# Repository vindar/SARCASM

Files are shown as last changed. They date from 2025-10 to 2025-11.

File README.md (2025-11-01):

# S.A.R.C.A.S.M
**Slightly Annoying Rubik's Cube Automatic Solving Machine**

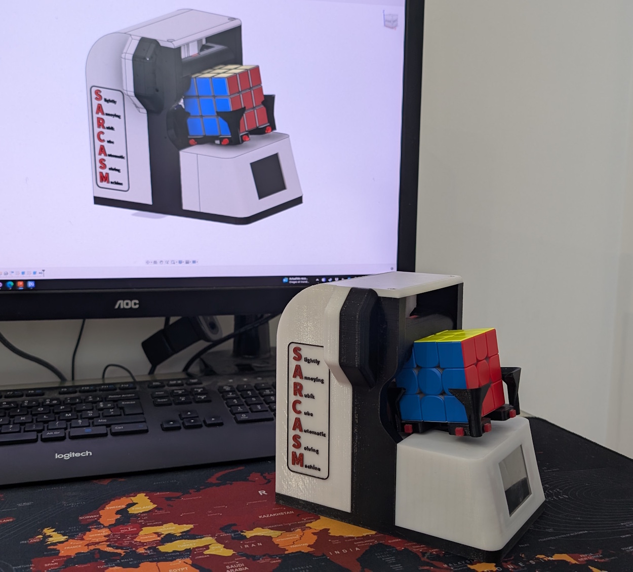
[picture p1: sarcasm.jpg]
S.A.R.C.A.S.M


*S.A.R.C.A.S.M* is a 3D-printed, Teensy-powered robot that scans, solves, and sassily comments on a Rubik’s Cube.  

This repository contains the code and schematics of the build.

Additional details may be found on the Teensy forum thread:

https://forum.pjrc.com/index.php?threads/sarcasm-an-over-engineered-rubiks-cube-solving-robot.77338/

## Demo videos
- Short clip: https://youtube.com/shorts/Xer4mPZZH8E
- Full demo: https://youtu.be/WV52RtuWXk0

## Highlights
- Teensy 4.1 main controller + ESP32-CAM for image capture.
- ILI9341 display with custom 2D&3D graphics, animations, and lip-sync.
- Stepper + servos for cube handling with position sensors to detect faults.  
- RGBW lighting synchronized to audio.
- On-device TTS (espeak-ng) with a collection of sarcastic lines.
- ...

## Note
A slight modification of Teensy's core is required in order for the whole code to fit in RAM. 

Edit `cores/teensy4/usb_serial.c` and `cores/teensy4/usb_serial2.c` and, in each file, remove the DMAMEM attribute in front of the definition of the `txbuffer[]` and `rx_buffer[]` arrays. 

## Warning
This is a work in progress. The repo is currently in a very messy and incomplete state (and will most likely stay that way until I find some time to work on it...). Sorry !

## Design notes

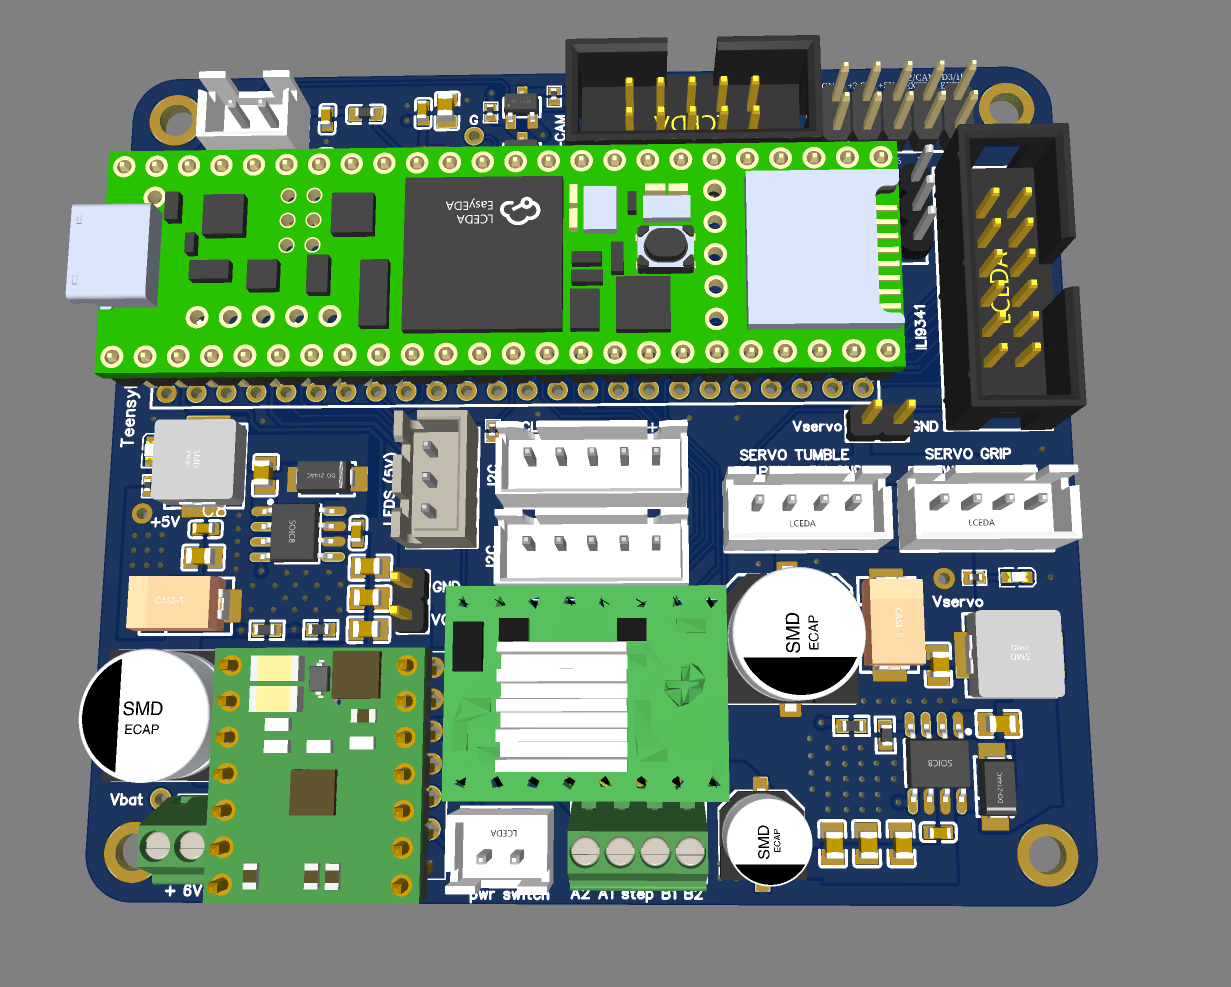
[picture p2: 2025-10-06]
Hardware/mainboard/3D.png

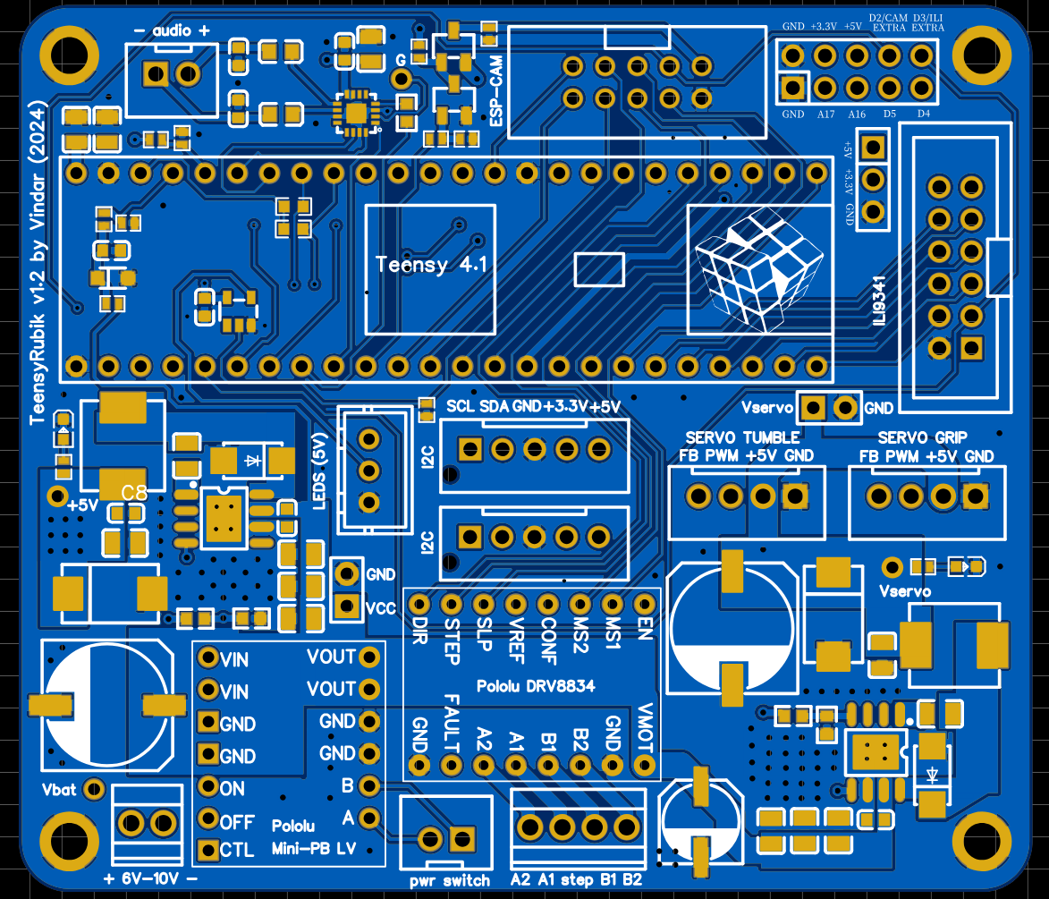
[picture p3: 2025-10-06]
Hardware/mainboard/Capture d'écran 2025-10-04 122526.png

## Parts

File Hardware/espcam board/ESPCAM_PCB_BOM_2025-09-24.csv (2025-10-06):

ID | Name | Designator | Footprint | Quantity | Manufacturer Part | Manufacturer | Supplier | Supplier Part | Price
1 | 68uF | C1,C3 | CAP-SMD_L6.0-W3.2-R-RD | 2 | TAJC686K016RNJ | Kyocera AVX | LCSC | C7220 | 0.317
2 | ESP32-CAM | CAM1 | ESP32CAM-SOCKET | 1 | https://github.com/raphaelbs/esp32-cam-ai-thinker | AI Thinker |  | https://github.com/raphaelbs/esp32-cam-ai-thinker
3 | KT-0603R | LED1 | LED0603-RD | 1 | KT-0603R | KENTO | LCSC | C2286 | 0.006
4 | IDC 2x5 | P1 | IDC-TH_10P-P2.54_C5665 | 1 | IDC Box 2.54mm 2X5P | BOOMELE | LCSC | C5665 | 0.075
5 | 2kΩ | R2 | R0402 | 1 | 0402WGF2001TCE | UNI-ROYAL(厚声) | LCSC | C4109 | 0.001
6 | 10K | R4 | R0603 | 1 | 0603WAF1002T5E | UniOhm | LCSC | C25804 | 0.001
7 | INMP441-MEMS-I2S-MIC-MODULE | U1 | INMP441-MEMS-I2S-MIC-MODULE | 1 |  |  | ebay

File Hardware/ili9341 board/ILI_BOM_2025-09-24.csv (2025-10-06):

ID | Name | Designator | Footprint | Quantity | Manufacturer Part | Manufacturer | Supplier | Supplier Part | Price
1 | 470uF | C5 | CAP-TH_BD8.0-P3.50-D1.0-FD | 1 | 01EC1227SHC470UF25V | KNSCHA | LCSC | C503221 | 0.053
2 | HDR 2.54mm 1x14 | CON1 | HDR 2.54MM 1X14 | 1 | HDR 2.54mm 1x14
3 | green | LED2 | LED0603-R-RD | 1 | 19-217/GHC-YR1S2/3T | EVERLIGHT | LCSC | C72043 | 0.022
4 | IDC 2x6 | P1 | IDC-TH_12P-P2.54_BOOMELE-2X6P-2.54MM | 1 | IDC Box 2X6 2.54MM | BOOMELE | LCSC | C9136 | 0.096
5 | 2K | R2 | R0603 | 1 | 0603WAF2001T5E | UniOhm | LCSC | C22975 | 0.001

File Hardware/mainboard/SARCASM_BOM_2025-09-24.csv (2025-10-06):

ID | Name | Designator | Footprint | Quantity | Manufacturer Part | Manufacturer | Supplier | Supplier Part | Price | JLCPCB Part Class | LCSC Assembly
1 | 100nF | C1,C21 | C0603 | 2 | CC0603KRX7R9BB104 | YAGEO(国巨) | LCSC | C14663 | 0.002 | Basic Part
2 | 22uF | C2,C3,C6,C12,C16,C17,C19,C23,C25,C26,C28 | C0805 | 11 | CL21A226MAQNNNE | SAMSUNG | LCSC | C45783 | 0.025 |  | Yes
3 | 1uF | C4,C5,C7,C8 | C0603 | 4 | CL10A105KB8NNNC | SAMSUNG(三星) | LCSC | C15849 | 0.005 | Basic Part
4 | 470uF | C9,C11 | CAP-SMD_BD10.0-L10.3-W10.3-RD | 2 | VZH471M1ETR-1010 | Lite-On Semicon | LCSC | C249933 | 0.152 |  | Yes
5 | 10nF | C13,C27 | C0805 | 2 | CL21B103KBANNNC | SAMSUNG | LCSC | C1710 | 0.006 |  | Yes
6 | 1nF | C15,C22 | C0603 | 2 | CL10B102KB8NNNC | SAMSUNG(三星) | LCSC | C1588 | 0.003 | Basic Part
7 | 220uF | C18,C24 | CAP-SMD_L7.3-W4.3-R-RD | 2 | 10TPE220ML | PANASONIC | LCSC | C147767 | 0.854 |  | Yes
8 | 100uF | C20 | CAP-SMD_BD6.3-L6.6-W6.6-RD | 1 | VES101M1ETR-0607 | LELON | LCSC | C176675 | 0.055 |  | Yes
9 | JST-XH | CN1,CN4 | CONN-TH_B2B-XH-A (LF)(SN) | 2 | - | JST Sales America | LCSC | C158012 | 0.035
10 | JST-XH | CN2,CN3 | CONN-TH_B5B-XH-AM-LF-SN | 2 | B5B-XH-AM(LF)(SN) | JST | LCSC | C161872 | 0.106 | Extended Part
11 | MM3Z10VST1G | D1 | SOD-323_L1.8-W1.3-LS2.5-RD | 1 | MM3Z10VST1G | ON Semicon | LCSC | C235983 | 0.039 |  | Yes
12 | SS34_C8678 | D2,D3 | DO-214AC_L4.3-W2.7-LS5.3-RD | 2 | SS34 | MDD | LCSC | C8678 | 0.028 |  | Yes
13 | HDR | H1,H2 | HDR-TH_2P-P2.54-V-M-1 | 2 | B-2100S02P-A110 | Ckmtw(灿科盟) | LCSC | C124375 | 0.025 | Extended Part
14 | 10uH | L1,L2 | IND-SMD_L7.1-W6.6 | 2 | MWSA0603-100MT | Sunlord | LCSC | C132141 |  |  | Yes
15 | 220Ω | L3,L4 | L0603 | 2 | MPZ1608S221ATA00 | TDK | LCSC | C76815 | 0.01
16 | KT-0603R | LED2,LED3 | LED0603-RD | 2 | KT-0603R | KENTO | LCSC | C2286 | 0.006 | Basic Part
17 | IDC 2x6 | P1 | IDC-TH_12P-P2.54_BOOMELE-2X6P-2.54MM | 1 | IDC Box 2X6 2.54MM | BOOMELE | LCSC | C9136 | 0.096
18 | IDC 2x5 | P3 | IDC-TH_10P-P2.54_C5665 | 1 | IDC Box 2.54mm 2X5P | BOOMELE | LCSC | C5665 | 0.075
19 | S8050 | Q1 | SOT-23-3_L3.0-W1.7-P0.95-LS2.9-BR | 1 | S8050 | CJ | LCSC | C2146 | 0.013 |  | Yes
20 | SI2301CDS-T1-GE3 | Q3 | SOT-23-3_L3.0-W1.7-P0.95-LS2.9-BR | 1 | SI2301CDS-T1-GE3 | VISHAY | LCSC | C10487 | 0.057 |  | Yes
21 | 10K | R1,R5 | R0402 | 2 | 0402WGF1002TCE | UniOhm | LCSC | C25744 | 0.001 |  | Yes
22 | 2K | R2,R10 | R0402 | 2 | 0402WGF2001TCE | UniOhm | LCSC | C4109 | 0.001 |  | Yes
23 | 33K | R3,R9,R13,R14,R24 | R0402 | 5 | 0402WGF3302TCE | UniOhm | LCSC | C25779 | 0.001 |  | Yes
24 | 1K | R4,R25 | R0402 | 2 | 0402WGF1001TCE | UniOhm | LCSC | C11702 | 0.001 |  | Yes
25 | 22K | R6 | R0402 | 1 | 0402WGF2202TCE | UniOhm | LCSC | C25768 | 0.001 |  | Yes
26 | 3.24K | R7,R20 | R0603 | 2 | 0603WAF3241T5E | UniOhm | LCSC | C22994 | 0.001 |  | Yes
27 | 10K | R8,R19 | R0603 | 2 | 0603WAF1002T5E | UniOhm | LCSC | C25804 | 0.001 |  | Yes
28 | 3kΩ | R11,R12 | R0603 | 2 | 0603WAF3001T5E | UNI-ROYAL(厚声) | LCSC | C4211 | 0.001 | Basic Part
29 | 620K | R22 | R0603 | 1 | 0603WAF6203T5E | UniOhm | LCSC | C23219 | 0.001 |  | Yes
30 | Pololu Mini Pushbutton Power Switch with Reverse Voltage Protection (LV) | U1 | MINI PUSHBUTTON POWER SWITCH WITH REVERSE VOLTAGE PROTECTION | 1
31 | SN74LV1T34DBVR | U3 | SOT-23-5_L2.9-W1.6-P0.95-LS2.8-BR | 1 | SN74LV1T34DBVR | TI(德州仪器) | LCSC | C100024 | 0.059 | Extended Part
32 | TPS5430DDAR | U4,U13 | SOIC-8_L5.0-W4.0-P1.27-LS6.0-BL-EP | 2 | TPS5430DDAR | TI | LCSC | C9864 | 0.35 |  | Yes
33 | Terminal Block | U5 | CONN-TH_P2.54_KF128-2.54-2P | 1 | KF128-2.54-2P | Cixi Kefa Elec | LCSC | C474920 | 0.219
34 | TEENSY4.1 | U6 | TEENSY 4.1 | 1 |  | PJRC
35 | JST-XH | U7 | CONN-TH_B4B-XH-A (LF)(SN) | 1 | B4B-XH-A(LF)(SN) | JST Sales America | LCSC | C144395 | 0.049
36 | JST XH | U8 | CONN-TH_B4B-XH-A (LF)(SN) | 1 | B4B-XH-A(LF)(SN) | JST Sales America | LCSC | C144395 | 0.049
37 | Pololu DRV8834 | U9 | DRV8834 STEPPER MOTOR DRIVER CARRIER | 1
38 | terminal block | U10 | CONN-TH_4P-P2.54_KF128-2.54-4P | 1 | KF128-2.54-4P | Cixi Kefa Elec | LCSC | C474922 | 0.448
39 | HDR | U11 | CONN-TH_3P-P2.50_A2501WV2-3P | 1 | B3B-XH-A(LF)(SN) | JST | LCSC | C144394 | 0.047 | Extended Part
40 | HDR 2x5 | U12 | HDR-TH_10P-P2.54-V-M-R2-C5-S2.54 | 1 | ZX-PZ2.54-2-5PZZ | Megastar(兆星) | LCSC | C7501276 | 0.041 | Extended Part
41 | HDR | U14 | HDR-TH_3P-P2.54-V-M | 1 | HB-PH3-25413PB2GOP | HANBO(汉博) | LCSC | C6332196 | 0.016 | Extended Part
42 | MAX98357AETE+T | U15 | TQFN-16_L3.0-W3.0-P0.50-BL-EP1.5 | 1 | MAX98357AETE+T | ADI(亚德诺)/MAXIM(美信) | LCSC | C910544 | 1.311 | Extended Part

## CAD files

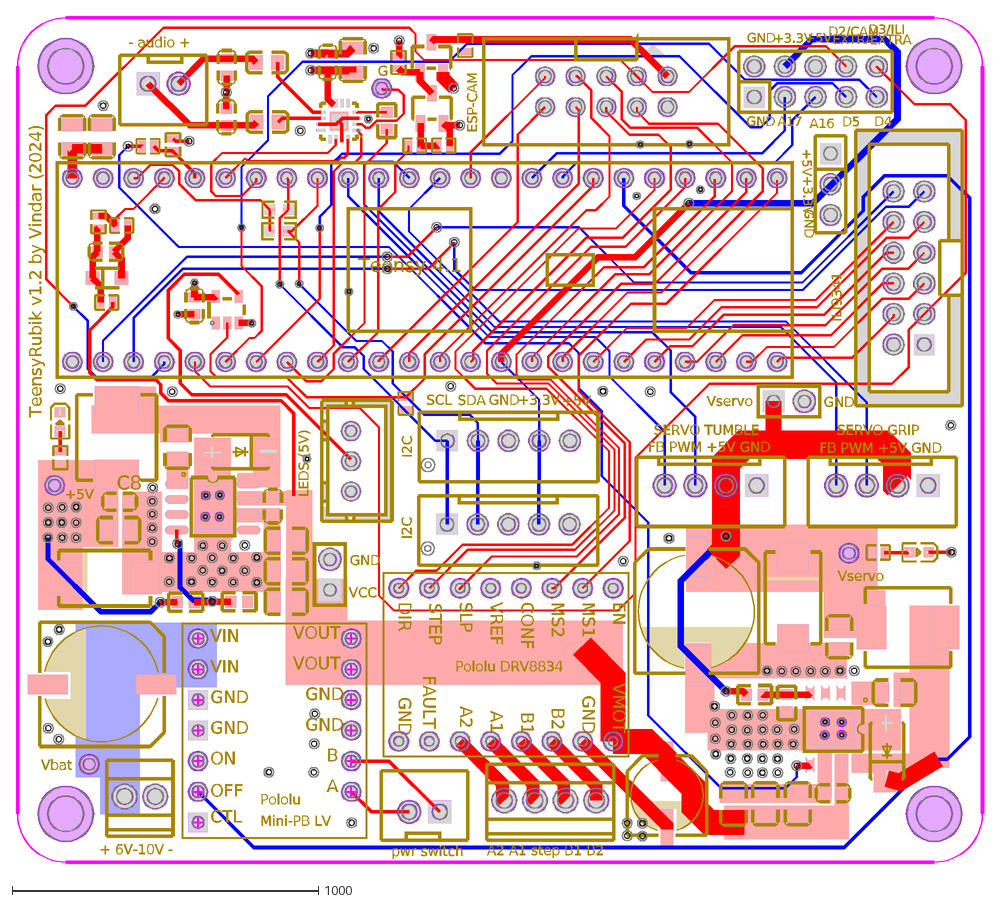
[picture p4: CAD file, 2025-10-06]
Hardware/mainboard/SARCASM_PCB_2025-09-24.dxf
GND
TeensyRubik v1.2 by Vindar (2024)
FB PWM +5V GND
Vservo
- audio +
ILI9341
ESP-CAM
Pololu
Pololu DRV8834
SERVO GRIP
SERVO TUMBLE
A2 A1 step B1 B2
pwr switch
Mini-PB LV
+ 6V-10V -
Vbat
VCC
+5V
Teensy 4.1
+3.3V
D2/CAM
D3/ILI
D4
D5
A17
A16
EXTRA
LEDS (5V)
I2C
SDA
SCL
G
C8
MS1
MS2
CONF
STEP
DIR
FAULT
A2
A1
B1
B2
VMOT
EN
VREF
SLP
VIN
ON
OFF
CTL
A
B
VOUT

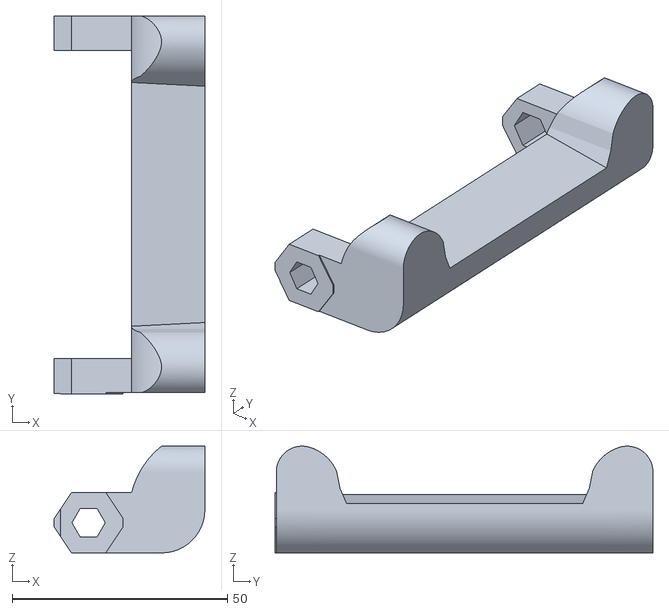
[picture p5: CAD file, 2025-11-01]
Hardware/STL/gripper_main_part.stl
35.0 x 87.8 x 24.8

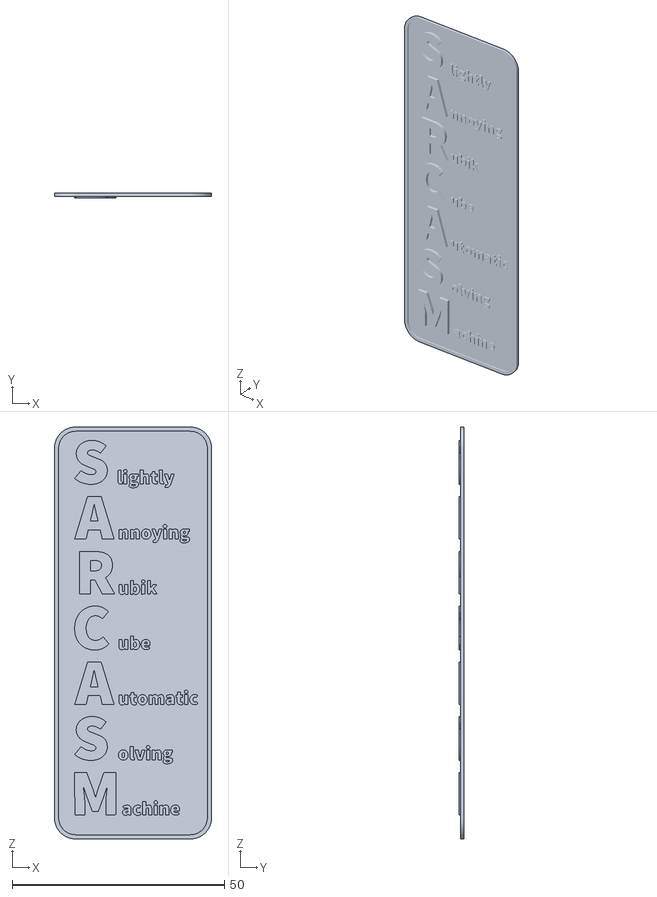
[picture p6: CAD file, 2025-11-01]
Hardware/STL/SARCASM_nametag_multicolor.stl
37.0 x 1.20 x 97.0

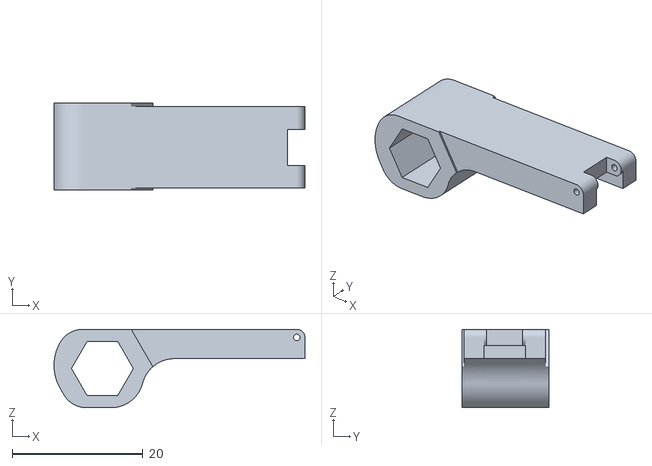
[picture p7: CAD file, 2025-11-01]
Hardware/STL/tumble_lever_main_part.stl
38.4 x 13.2 x 12.0

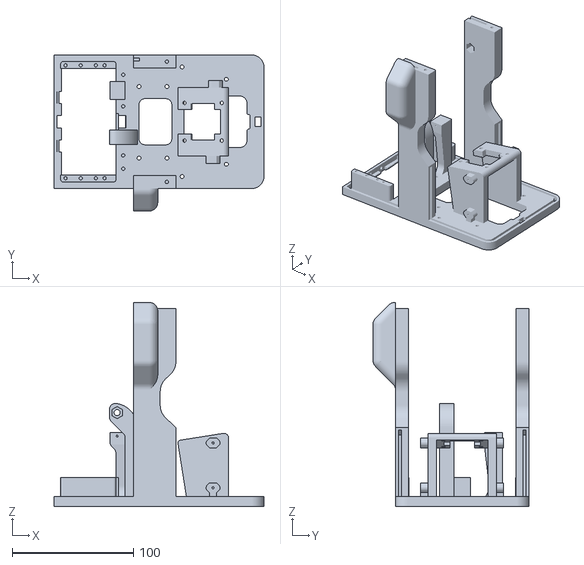
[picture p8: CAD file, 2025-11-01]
Hardware/STL/main_frame.stl
173.0 x 128.5 x 168.1

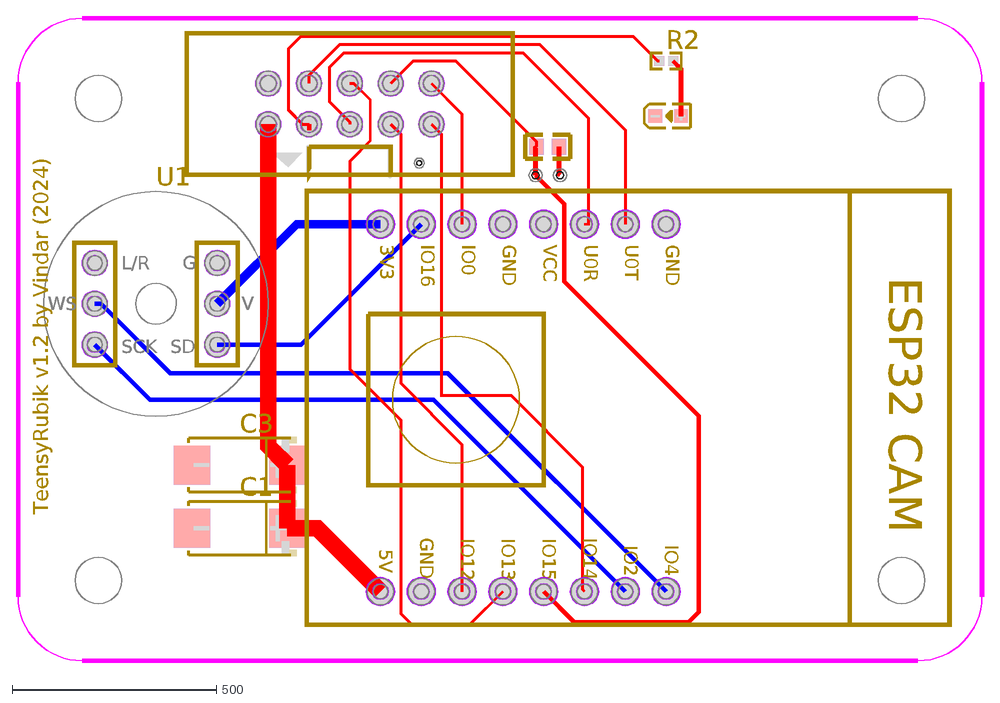
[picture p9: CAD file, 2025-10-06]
Hardware/espcam board/ESPCAM_PCB_2025-09-24.dxf
TeensyRubik v1.2 by Vindar (2024)
C1
C3
R2
U1
G
V
SD
SCK
WS
L/R
GND
ESP32 CAM
U0T
U0R
VCC
IO0
IO16
3V3
5V
IO12
IO13
IO15
IO14
IO2
IO4

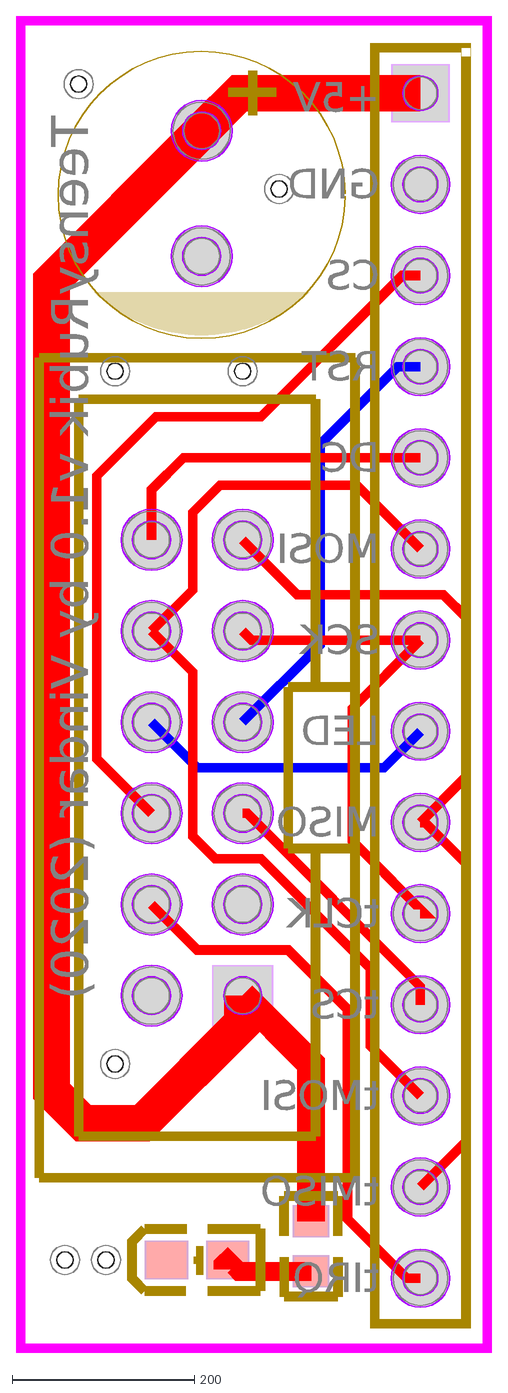
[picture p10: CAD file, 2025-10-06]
Hardware/ili9341 board/ILI9341_PCB_2025-09-24.dxf
TeensyRubik v1.0 by Vindar (2020)
GND
+5V
CS
RST
DC
MOSI
SCK
LED
MISO
tCLK
tCS
tMOSI
tMISO
tIRQ

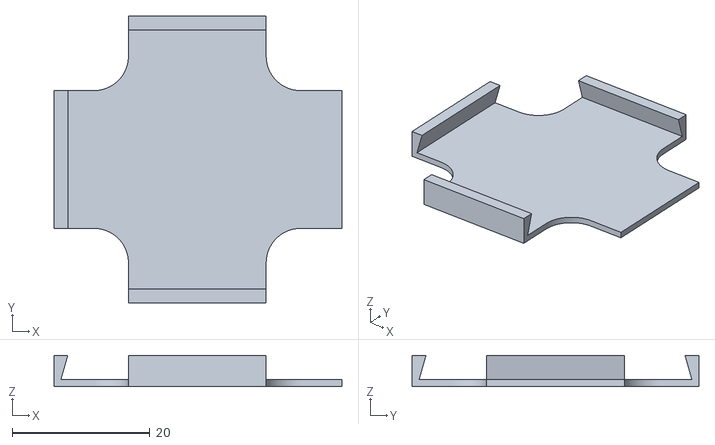
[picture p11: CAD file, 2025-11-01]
Hardware/STL/AS5600_holder_cover.stl
41.8 x 41.6 x 4.50

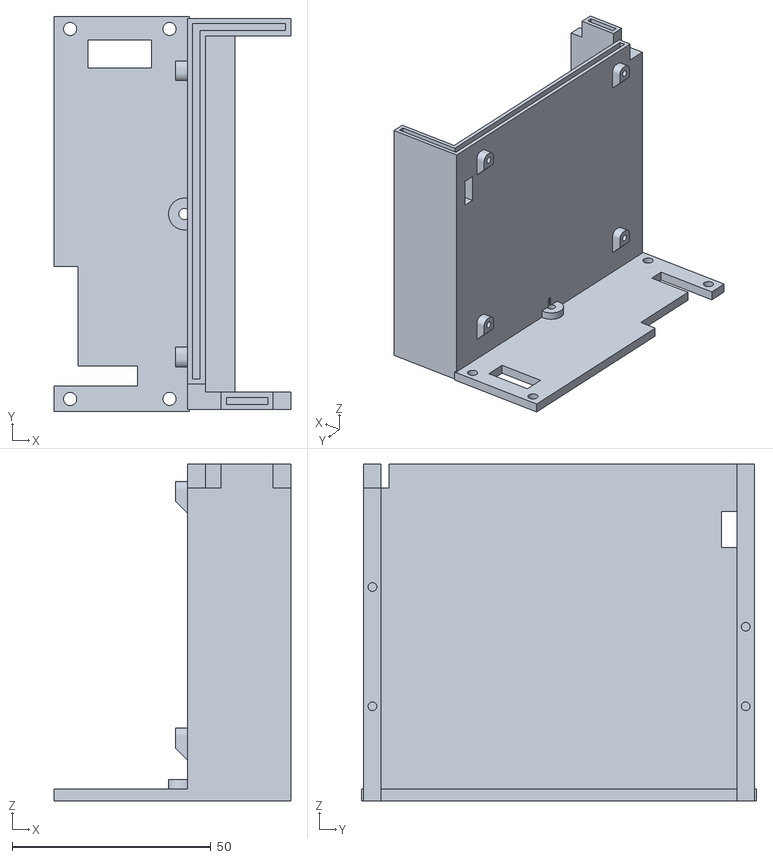
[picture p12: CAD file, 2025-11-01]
Hardware/STL/separator_wall_bottom_part.stl
59.5 x 99.4 x 84.7

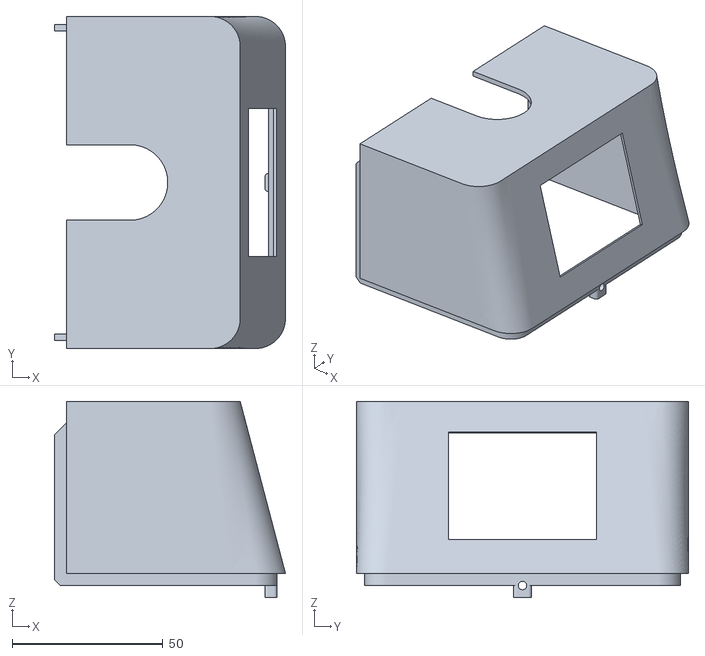
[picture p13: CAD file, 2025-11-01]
Hardware/STL/front_cover.stl
76.5 x 110.0 x 65.0

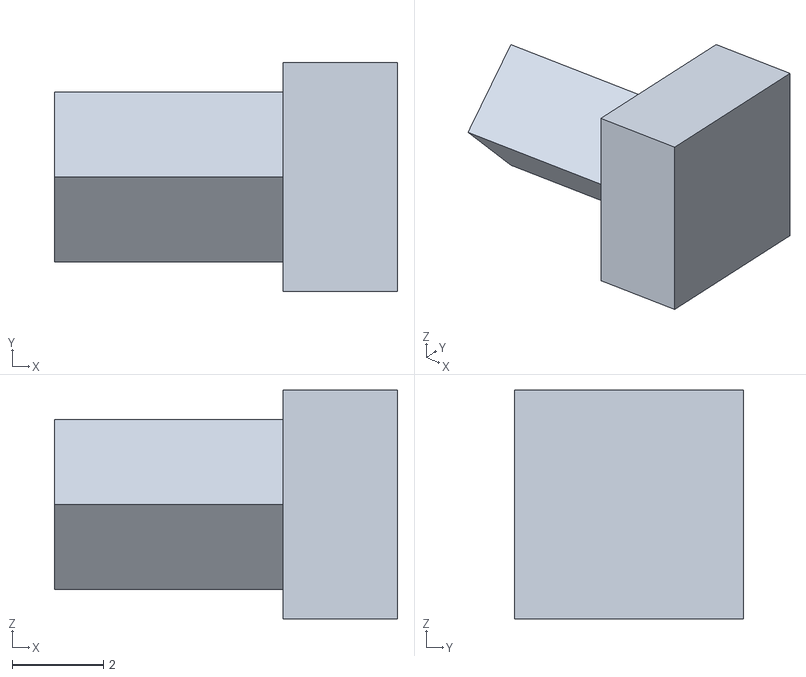
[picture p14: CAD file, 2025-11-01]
Hardware/STL/cube_cradle_red_marker_x8.stl
7.50 x 5.00 x 5.00

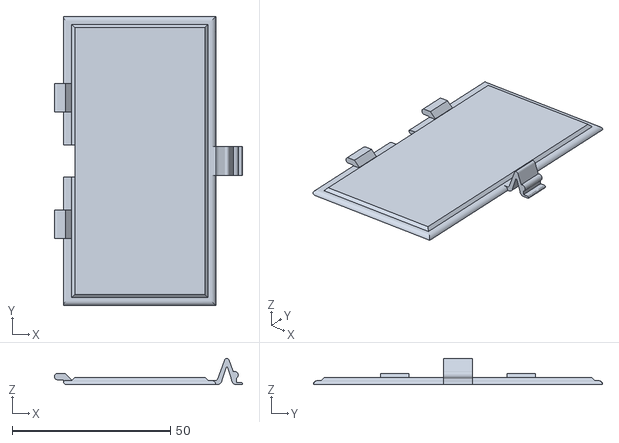
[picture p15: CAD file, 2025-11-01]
Hardware/STL/battery_trap_cover.stl
59.4 x 91.2 x 8.25

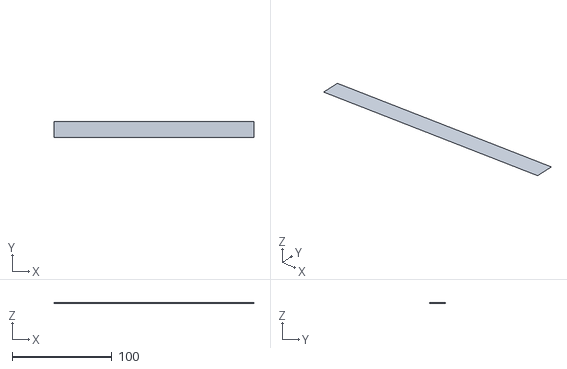
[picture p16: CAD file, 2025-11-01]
Hardware/STL/flexible_led_cover.stl
200.0 x 16.0 x 0.3

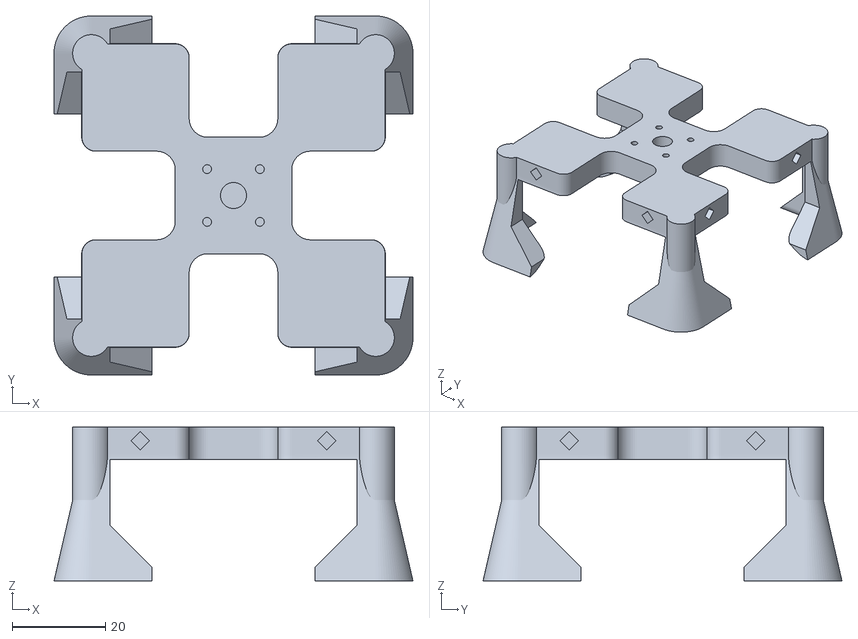
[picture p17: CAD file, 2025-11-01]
Hardware/STL/cube_cradle.stl
77.0 x 77.0 x 33.0

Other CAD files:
Hardware/STL/espcam_arm_right.stl
Hardware/STL/tumble_lever_tip.stl
Hardware/STL/gripper_color_indicator.stl
Hardware/STL/tumble_cover_left.stl
Hardware/STL/AS5600_holder.stl
Hardware/STL/back_cover.stl
Hardware/STL/espcam_arm_left.stl
Hardware/STL/foot_back_TPU_x2.stl
Hardware/STL/foot_front_1_TPU_x2.stl
Hardware/STL/gripper_nut.stl
Hardware/STL/gripper_screw.stl
Hardware/STL/gripper_servo_nut.stl
Hardware/STL/pololu_usb_connector_holder.stl
Hardware/STL/separator_wall_top_part.stl
Hardware/STL/tumble_cover_right.stl
Hardware/STL/tumble_holding_screw.stl
Hardware/STL/tumble_servo_nut.stl

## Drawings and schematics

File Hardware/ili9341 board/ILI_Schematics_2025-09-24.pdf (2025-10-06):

A | A

1

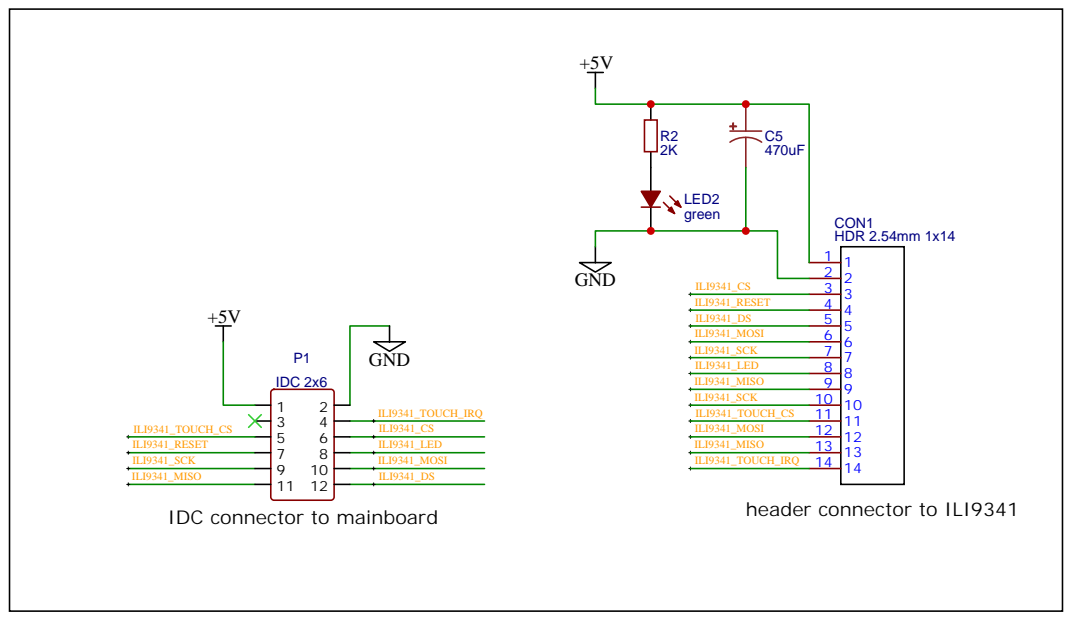
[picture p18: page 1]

ILI9341_SCK
IDC connector to mainboard

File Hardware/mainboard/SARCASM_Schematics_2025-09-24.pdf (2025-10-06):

A | A
B | B

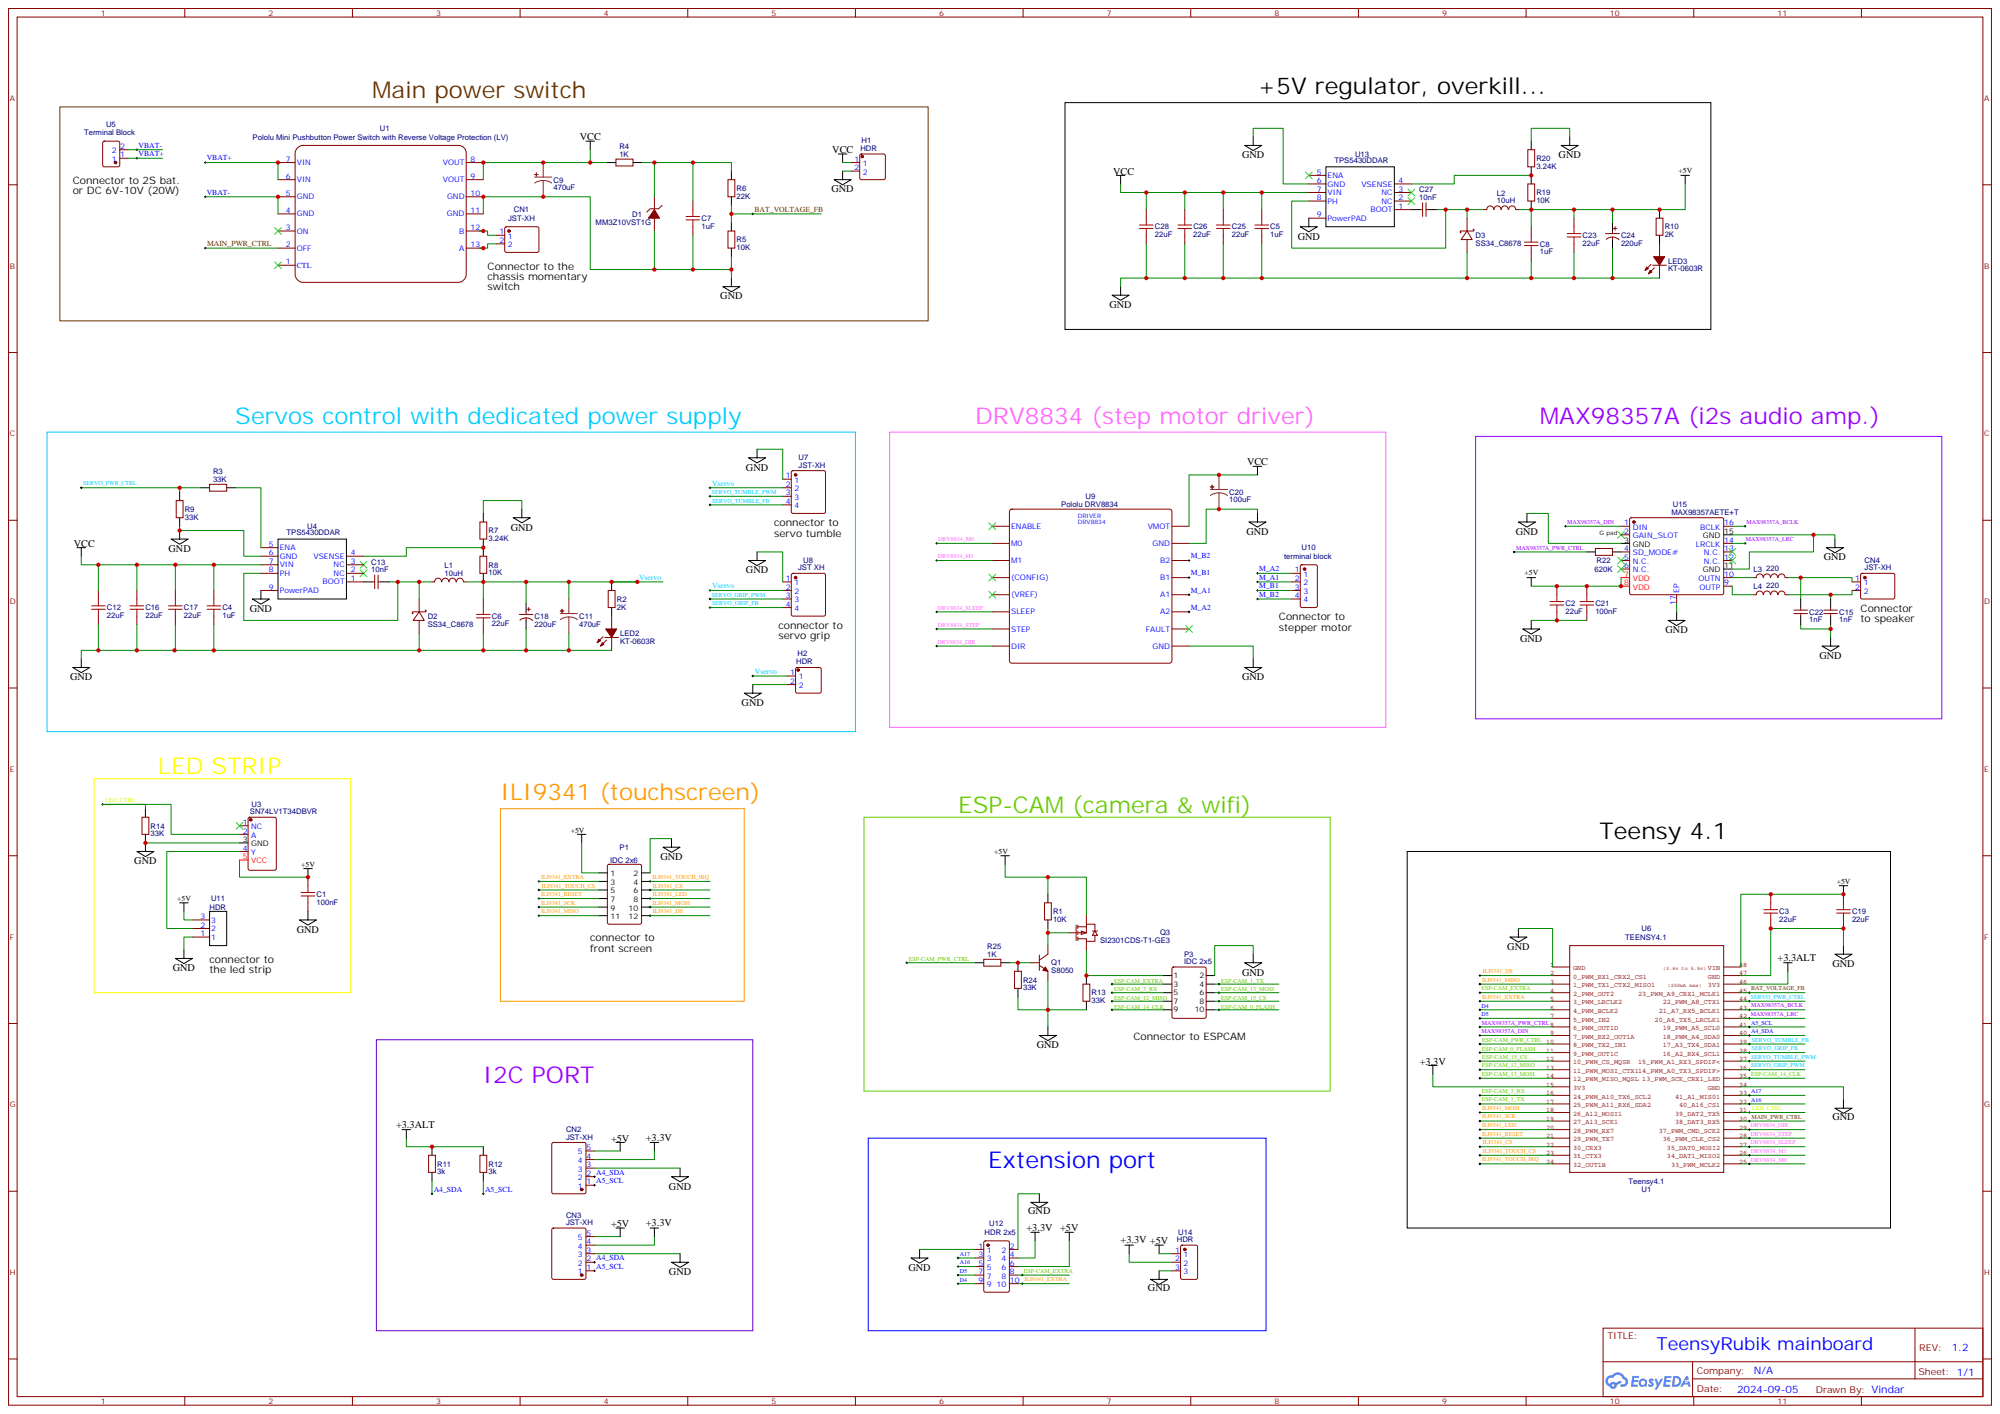
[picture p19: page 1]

Pololu Mini Pushbutton Power Switch with Reverse Voltage Protection (LV)

Servos control with dedicated power supply

ESP-CAM (camera & wifi)

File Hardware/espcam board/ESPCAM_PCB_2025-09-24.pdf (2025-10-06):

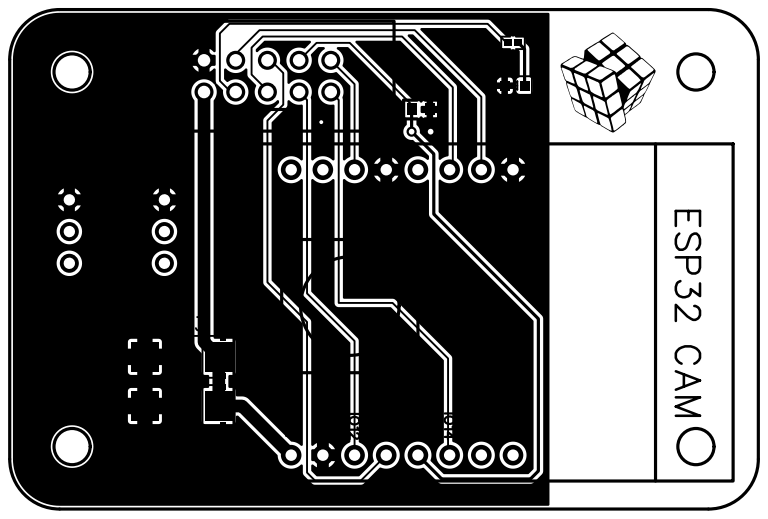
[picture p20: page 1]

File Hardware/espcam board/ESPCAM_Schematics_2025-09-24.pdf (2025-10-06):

A | A

1

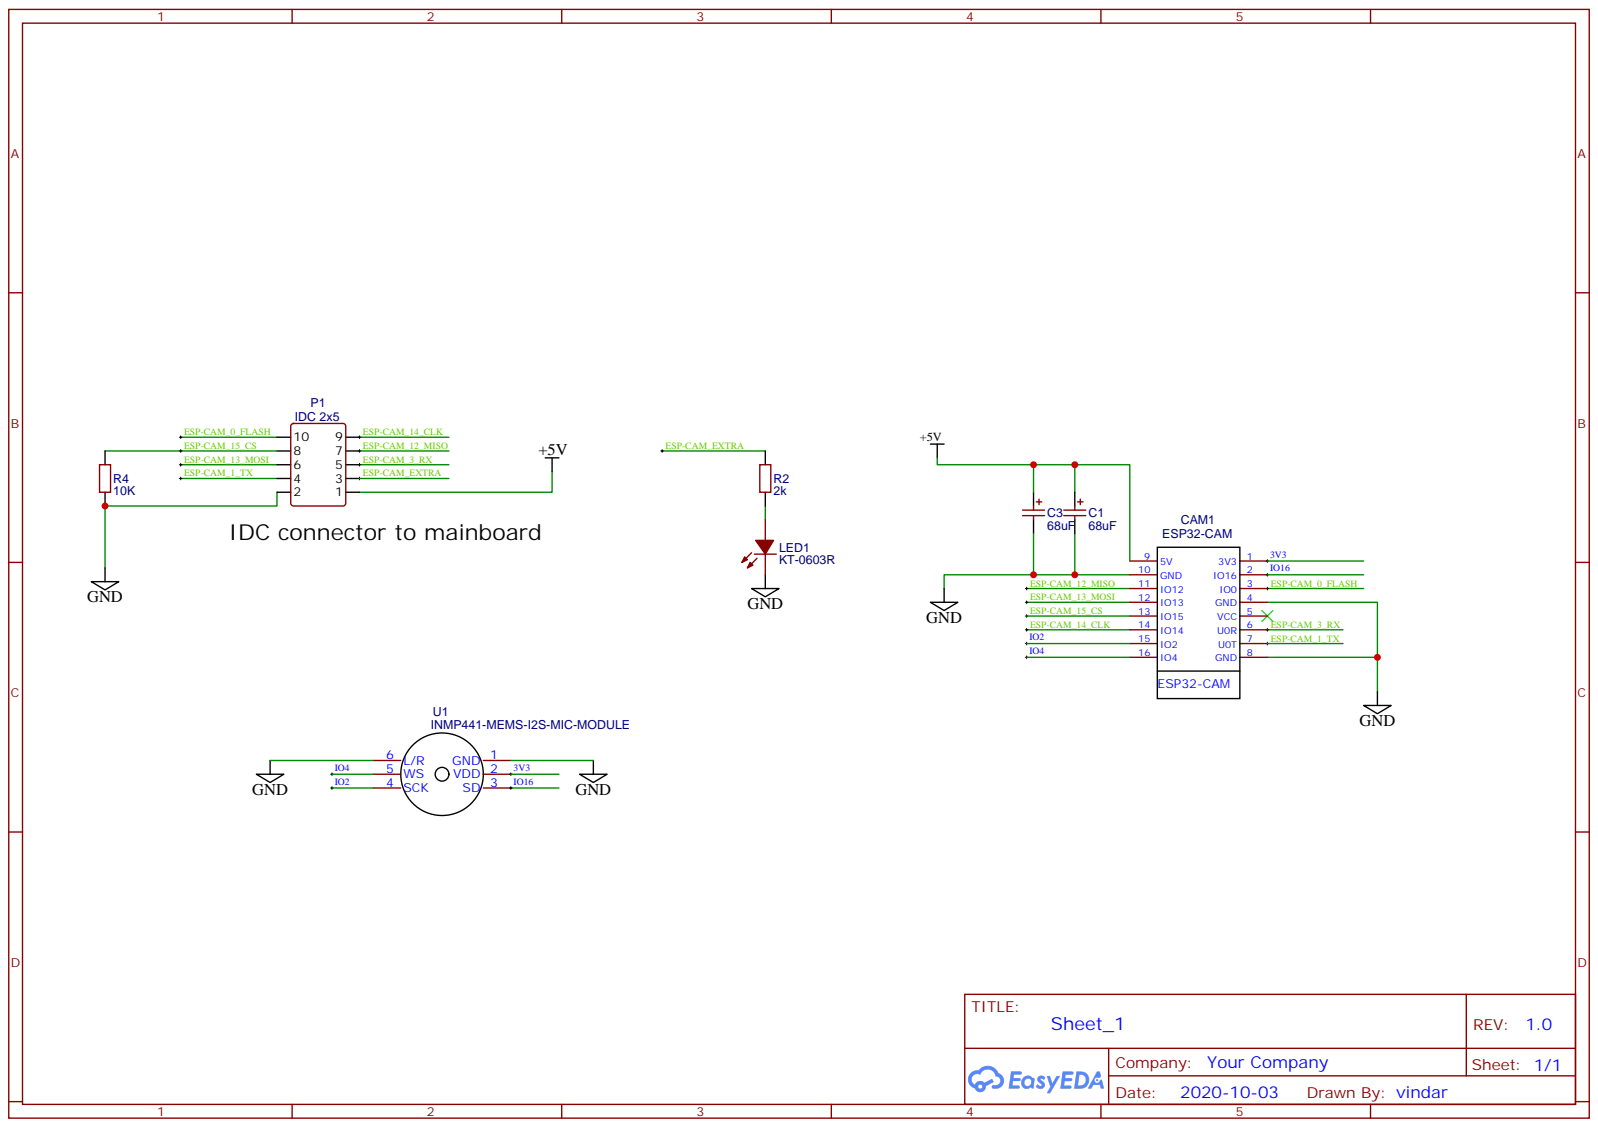
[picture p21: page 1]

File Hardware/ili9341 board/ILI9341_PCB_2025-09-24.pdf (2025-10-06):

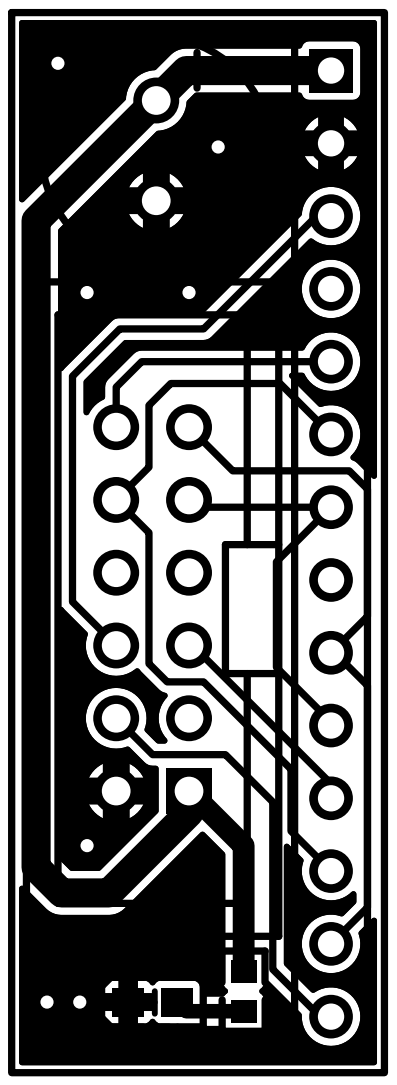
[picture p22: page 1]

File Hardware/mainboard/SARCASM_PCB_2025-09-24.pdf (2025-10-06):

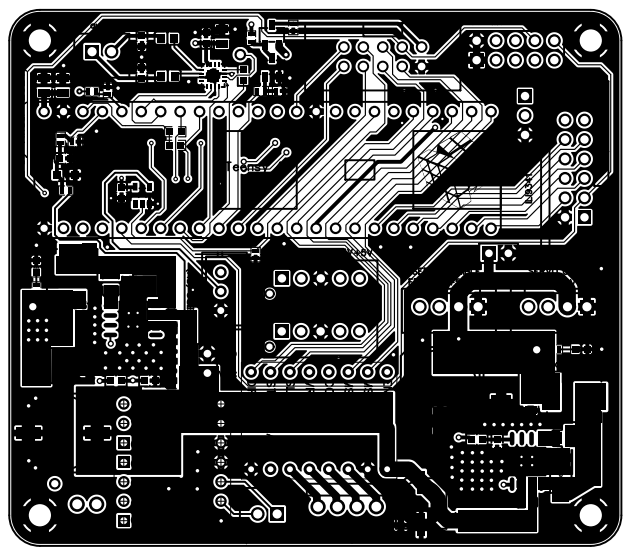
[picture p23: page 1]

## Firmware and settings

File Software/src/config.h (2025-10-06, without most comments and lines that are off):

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
#pragma once
#include <Arduino.h>
#define ENABLE_DEBUG_VIA_SERIAL 1
#ifdef CDC2_DATA_INTERFACE // c.f. usb_desc.h
    #define _DEBUG_SERIAL	SerialUSB1  // use the second USB serial for debugging
#else
    #if ENABLE_DEBUG_VIA_SERIAL
    #ifdef __cplusplus
    #warning "Debug disabled, please select 'USB Type Dual Serial' in the compiler settings"
    #endif
    #endif
    #undef ENABLE_DEBUG_VIA_SERIAL
    #define ENABLE_DEBUG_VIA_SERIAL 0   // no debug serial port available : disable debbuging
#endif
#define TEENSYTHREADS_SLICE_US 40
#define TEENSYTHREADS_DEFAULT_TICKS 10
#define DEBUG_MEMORY 1
#define RUN_SLOWFUN_FROM_FLASH 1
#if (RUN_SLOWFUN_FROM_FLASH)
#define SLOWFUN FLASHMEM
#else
#define SLOWFUN
#endif
#define PANIC_POWEROFF_DELAY_MS 20000
#define CUTOFF_VOLTAGE_MAX	9.0f
#define CUTOFF_VOLTAGE_MIN	6.2f
#define VOLTAGE_THRESHOLD_LOW 7.4f
#define VOLTAGE_PANIC_SAMPLES 10
#define CHARGING_STATUS_TIMEOUT 4000 // time (ms) without change before changing the charging status
#define CHARGING_CURRENT_SLOW 0.2f // below this current, we consider we are not charging
#define CHARGING_CURRENT_FAST 0.8f // below this current, we consider we are slow charging
#define LED_CONFIG (WS2811_GRBW | WS2811_800kHz) //uses SK6812 (GRBW) leds. 800kHz data rate.
#define BASICMOVES_STACK_SIZE        4096
#define BASICMOVES_TUMBLE_TIME_MS    1000
#define BASICMOVES_CLOSEGRIP_TIME_MS 1000
#define BASICMOVES_OPENGRIP_TIME_MS  1000
#define SERVO_PWM_HALFPERIOD  10000
#define SERVO_DEFAULT_STALL_DELTA 10        // value under which we consider the servo has not move (to increase the stall count)
#define SERVO_DEFAULT_REACH_TOLERANCE 70    // value under which we consider to have reached the position
#define SERVO_DEFAULT_PANIC_TOLERANCE 70    // value over which we stop the servo and start the panic mode when stalled (must be larger than SERVO_DEFAULT_REACH_TOLERANCE)
#define SERVO_TUMBLE_MSG_QUEUE_SIZE 12
#define SERVO_GRIP_MSG_QUEUE_SIZE 12
#define SERVO_TUMBLE_MIN_PULSE  450     // hardware values: set before full calibration procedure
#define SERVO_TUMBLE_MAX_PULSE  2200    // MIN : tumble dow, MAX : tumble up
#define SERVO_TUMBLE_MIN_V_FB  657      // values set after the full calibration procedure.
#define SERVO_TUMBLE_MAX_V_FB  3025     //
#define SERVO_TUMBLE_CALIB_TOLERANCE 150 // tolerance when performing fast offset calibration (previous 100)
#define SERVO_TUMBLE_STALL_COUNT_REACHED    3   // number of consecutive read to declare stall at position
#define SERVO_TUMBLE_STALL_COUNT_AWAY       6   // number of consecutive read to declare stall away from position
#define SERVO_TUMBLE_STALL_COUNT_PANIC      12  // number of consecutive read to declare stall panic
#define SERVO_TUMBLE_REST_POS 1880        // rest (safe) position for the tumble servo
#define SERVO_TUMBLE_REST_MIN 1780        // minimum safe value
#define SERVO_TUMBLE_CUBE_TOUCH 1550      // position where the tumble start touching the cube
#define SERVO_TUMBLE_CUBE_UPRIGHT 650     // posiiton upright of the tumble
#define SERVO_TUMBLE_CUBE_SPEED_UP 60     // speed when going up during a tumble
#define SERVO_TUMBLE_CUBE_SPEED_DOWN 90   // speed when going down during a tumble
#define SERVO_GRIP_MIN_PULSE  670      // hardware values: set before full calibration procedure
#define SERVO_GRIP_MAX_PULSE  2030     // MIN : grip down, MAX = grip up
#define SERVO_GRIP_MIN_V_FB  976      // values set after the full calibration procedure.
#define SERVO_GRIP_MAX_V_FB  2760     //
#define SERVO_GRIP_CALIB_TOLERANCE 150 // tolerance when performing fast offset calibration
#define SERVO_GRIP_STALL_COUNT_REACHED    3   // number of consecutive read to declare stall at position
#define SERVO_GRIP_STALL_COUNT_AWAY       8   // number of consecutive read to declare stall away from position
#define SERVO_GRIP_STALL_COUNT_PANIC      14  // number of consecutive read to declare stall panic
#define SERVO_GRIP_STORE_POS  1950      // value for the grip when it is at rest, safe and "stored" for a long time
#define SERVO_GRIP_REST_POS   1500      // value for the grip when it is at rest (safe position)
#define SERVO_GRIP_REST_MIN   1400      // minimum safe value (below this, we may touch when umbling/turning)
#define SERVO_GRIP_CUBE_TOUCH_MIN  730  // minimum position where the grip can touch the cube
#define SERVO_GRIP_CUBE_TOUCH_MAX  1000 // maximum position where the grip can touch the cube
#define SERVO_GRIP_CUBE_TOUCH_OFF  5    // offset to the cube position to prevent bumping into it
#define DRV8834_STEPS_MICROSTEPPING      16
#define DRV8843_STEPS_FREQ               4000
#define DRV8834_TURN_MICROSTEPPING      16
#define DRV8843_TURN_FREQ_START_DEFAULT       4000 // 5000
#define DRV8843_TURN_FREQ_MAX_DEFAULT         10000 // 12000
#define DRV8843_TURN_ALPHA_DEFAULT            0.3f // 0.2f
#define DRV8843_TURN_FREQ_START_90DEG       4000
#define DRV8843_TURN_FREQ_MAX_90DEG         10000
#define DRV8843_TURN_ALPHA_90DEG            0.3f // 0.2f
#define DRV8843_TURN_FREQ_START_180DEG       4000
#define DRV8843_TURN_FREQ_MAX_180DEG         14000
#define DRV8843_TURN_ALPHA_180DEG            0.2f // 0.2f
#define DRV8843_TURN_FREQ_START_KOCIEMBA       4000
#define DRV8843_TURN_FREQ_MAX_KOCIEMBA         30000
#define DRV8843_TURN_ALPHA_KOCIEMBA            0.25f
#define DRV8834_INVERT_DIR              true
#define DRV8834_CLOCKWISE_DIR           (DRV8834_INVERT_DIR ? 1 : -1)
#define DRV8834_ANTICLOCKWISE_DIR       (DRV8834_INVERT_DIR ? -1 : 1)
#define DRV8834_CLOCKWISE_OVERSHOOT_ANGLE   10.0f
#define DRV8834_ANTICLOCKWISE_OVERSHOOT_ANGLE   10.0f
#define DRV8834_DEFAULT_OVERSHOOT_ANGLE -1.0f
#define DRV8834_WAIT_AFTER_ENABLE_MS 50
#define DRV8834_WAIT_BEFORE_DISABLE_MS 50
#define DRV8834_AS5600_OFFSET_0DEG 7
#define DRV8834_AS5600_OFFSET_90DEG 1040
#define DRV8834_AS5600_OFFSET_180DEG 2048
#define DRV8834_AS5600_OFFSET_270DEG 3085
#define DRV8834_AS5600_ANGLE_ERROR 0.8f // maximum admissible angle error at end of turn w.r.t the target angle: if larger, repositioning is required
#define DRV8834_AS5600_ANGLE_PANIC 10.0f // maximum admissible angle error before trigerring panic mode
#define DRV8834_AS5600_ANGLE_PANIC_FAST_MOVE 60.0f // maximum admissible angle error before trigerring panic mode when rotating very fast.
#define DRV8834_AS5600_NB_PANIC_MEASURES 4 // number of consecutive measures above DRV8834_AS5600_ANGLE_PANIC to declare panic mode.
#define CRADDLE_NO_POS 1000 // value representing unknown craddle position
#define	JD_SZBUF		1024 // default 512
#define JD_FORMAT		0
#define	JD_USE_SCALE	1
#define JD_TBLCLIP		0
#define JD_FASTDECODE	1
#define ESPCAM_SERIAL_SPEED 500000
#define ESPCAM_SPI_SPEED 60000000
#define ESPCAM_RX_buffer_size       1024
#define ESPCAM_SerialPacket_buffer_size   2048
#define ESPCAM_TJPGD_WORK_SIZE  4096
#define ESPCAM_SPI_CHUNK_SIZE   (JD_SZBUF * 4)
#define ESPCAM_SPI_CHUNK_TRAILING 16
#define ESPCAM_DMA_RETRY_US 10000
#define ESPCAM_POWERCYCLING_DELAY_MS 1000
#define ESPCAM_POWERCYCLING_CHECK_MS 100
#include "ESPCAMConfig.h"  // includes enum for framesizes
#define ESPCAM_CAMERA_CONFIG_FRAMESIZE      ESPCAM_RES_800x600
#define ESPCAM_CAMERA_CONFIG_FRAMESIZE_LX   800
#define ESPCAM_CAMERA_CONFIG_FRAMESIZE_LY   600
#define ESPCAM_CAMERA_CONFIG_QUALITY        5 // bonne qualité
#define ESPCAM_CAMERA_CONFIG_AWB            0 // s->set_whitebal(s, 0); Désactive la balance des blancs auto
#define ESPCAM_CAMERA_CONFIG_AWB_GAIN       0 // s->set_awb_gain(s, 0); Désactive le gain RGB auto
#define ESPCAM_CAMERA_CONFIG_AEC            0 // s->set_exposure_ctrl(s, 0);  Désactive l’exposition automatique
#define ESPCAM_CAMERA_CONFIG_AGC            0 // s->set_gain_ctrl(s, 0); Désactive le gain automatique
#define ESPCAM_CAMERA_CONFIG_WB_MODE        0  // s->set_wb_mode(s, 0);  Mode auto désactivé (inutile si whitebal=0)
#define ESPCAM_CAMERA_CONFIG_AEC_VALUE      140 // Exposition manuelle: ajuste si trop sombre/clair (0 a 1200) plus grand = plus lent.
#define ESPCAM_CAMERA_CONFIG_AGC_GAIN       0   // s->set_agc_gain(s, 0); gain electronique (mettre 0 et augmenter plutot le temps d'expo avec AEC_VALUE)
#define ESPCAM_CAMERA_CONFIG_GAINCEILING    0  // Ignoré puisque AGC off
#define ESPCAM_CAMERA_CONFIG_AEC2           0  // s->set_aec2(s, c0) ignoré car ESPCAM_CAMERA_CONFIG_AEC = 0
#define ESPCAM_CAMERA_CONFIG_AE_LEVEL       0  // s->set_ae_level(s, 0) ignoré car ESPCAM_CAMERA_CONFIG_AEC = 0
#define ESPCAM_CAMERA_CONFIG_BPC            1  // correction des pixels noirs
#define ESPCAM_CAMERA_CONFIG_WPC            1  // correction des pixels blanc
#define ESPCAM_CAMERA_CONFIG_RAW_GMA        1  // correction du gamma
#define ESPCAM_CAMERA_CONFIG_LENC           1  // Correction lentille activée
#define ESPCAM_CAMERA_CONFIG_BRIGHTNESS     0 // 0 = neutre (-2 a 2)
#define ESPCAM_CAMERA_CONFIG_CONTRAST       0 // 0 = neutre (-2 a 2)
#define ESPCAM_CAMERA_CONFIG_SATURATION     0 // 0 = neutre (-2 a 2)
#define ESPCAM_CAMERA_CONFIG_DCW            1 // 0 = pas de DCW (DCT) (1 = DCW activé)
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

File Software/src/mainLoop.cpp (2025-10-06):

//
// Copyright 2021 Arvind Singh
//
// This file is part of the S.A.R.C.A.S.M. source code.
//
// This is a free software: you can redistribute it and/or modify
// it under the terms of the GNU General Public License as published by
// the Free Software Foundation, either version 3 of the License, or
// (at your option) any later version.
//
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


#include <Arduino.h>
#include <TeensyThreads.h>

#include "mainLoop.h"

#include "config.h"
#include "Hardware.h"
#include "debug.h"
#include "Memory.h"
#include "PowerCtrl.h"
#include "debug.h" 
#include "panic.h"

#include "display.h"
#include "CraddleMove.h"
#include "Xorshift32.h"
#include "graphics3D.h"
#include "audioMAX98357A.h"
#include "AudioLed.h"
#include "Console.h"
#include "FBSensors.h"
#include "PowerCtrl.h"

#include "sentences.h"
#include "transition_tags.h"
#include "songs.h"
#include "RepeatSolvingAnimation.h"
#include "DreamingAnimation.h"
#include "idleSolveAnimation.h"
#include "BatteryAnimation.h"
#include "solveCube.h"
#include "shutdownSequence.h"









enum class Mood
    {
    MOOD_CURIOUS,
    MOOD_PLAYFUL,
    MOOD_LOGIC,
    MOOD_EXISTENTIAL,
    MOOD_HAUNTING,
    MOOD_DRYLOGIC,
    MOOD_MOCKING
    };

enum class Animation
    {
    ANIM_NONE,
    ANIM_REPLAY,
    ANIM_DREAMING,
    ANIM_IDLESOLVE,
    };



struct SarcasmState
    {

    SarcasmState() : _mood(Mood::MOOD_CURIOUS), _timeMoodChange(-1),
                     _timeInput(-1), _timeCradleMove(-1), _lastInputCode(CODE_NOTHING),
                     _nbSolves(0), _lastSolveDifficulty(0), _timeLastSolve(-1),
                     _nbAnimationsReplay(0), _timeReplay(-1),
                     _nbAnimationsDreaming(0), _timeDreaming(-1),
                     _nbAnimationsIdleSolve(0), _timeIdleSolve(-1),
                     _lastAnimationPlayed(Animation::ANIM_REPLAY), _timeAnimation(-1),
                     _timeBatteryAnimation(-1)
        {
        }


    /*--- MOOD ---*/
    Mood _mood; 
    int  _timeMoodChange; // time in ms since the last mood change.
    int _nbSpeechSameMood; // number of consecutive speeches in the same mood.

    Mood   currentMood() { return _mood; }
    int    timeSinceMoodChange() { return (_timeMoodChange < 0) ? _timeMoodChange : (int)(millis() - _timeMoodChange); }
    void   setMood(Mood m) { if (m != _mood) { _mood = m; _timeMoodChange = millis(); _nbSpeechSameMood = 0; } }
    void   incSpeechSameMood() { _nbSpeechSameMood++; }
    int    nbSpeechSameMood() { return _nbSpeechSameMood; }

    /*--- USER INPUT ---*/

    int _timeInput;  // time in ms since the last user input (touch, cradle or plug/unplug detected).
    int _timeCradleMove; // time since the last cradle move.
    int _lastInputCode;             // last input code (CODE_TOUCHED_SCREEN, CODE_SPINNED, CODE_CHARGING_START, CODE_CHARGING_STOP)

    int    timeSinceInput() { return (_timeInput < 0) ? _timeInput : (int)(millis() -_timeInput); }
    int    timeSinceCradleMove() { return (_timeCradleMove < 0) ? _timeCradleMove : (int)(millis() - _timeCradleMove); }
    int    lastInputCode() { return _lastInputCode; }
    void   setInput(int code)
        {
        if ((code != CODE_NOTHING) && (code != CODE_CHARGING_START) && (code != CODE_CHARGING_STOP))
            {
            _timeInput = millis();
            if (code == CODE_SPINNED) { _timeCradleMove = _timeInput; }
            _lastInputCode = code;
            }
        }

    /*--- SOLVES ---*/

    int _nbSolves;                  // number of solve performed
    int _solveNbMoves;              // number of moves in the last solve
    int _lastSolveDifficulty;       // last solve difficulty (impossible, easy, normal, already solved)
    int _timeLastSolve;             // time in ms since the last solve

    int    nbSolves() { return _nbSolves; }
    int    lastSolveDifficulty() { return _lastSolveDifficulty; }
    int    timeSinceLastSolve() { return (_timeLastSolve < 0) ? _timeLastSolve : (int)(millis() - _timeLastSolve); }
    int    lastSolveNbMoves() { return _solveNbMoves; }
    void   setSolve(int difficulty, int nbmoves) { _nbSolves++; _solveNbMoves = nbmoves; _lastSolveDifficulty = difficulty; _timeLastSolve = millis(); }

    /*--- ANIMATIONS ---*/

    int _nbAnimationsReplay;        // number of replay animations performed
    int _timeReplay; 
    int _nbAnimationsDreaming;      // number of dreaming animations performed
    int _timeDreaming;
    int _nbAnimationsIdleSolve;     // number of idleSolve animations performed
    int _timeIdleSolve;
    Animation _lastAnimationPlayed; // last animation played (replay, dreaming, idleSolve)
    int _timeAnimation;
    int _timeBatteryAnimation;      // time in ms since the last battery animation

    int    nbAnimationsReplay() { return _nbAnimationsReplay; }
    int    nbAnimationsDreaming() { return _nbAnimationsDreaming; }
    int    nbAnimationsIdleSolve() { return _nbAnimationsIdleSolve; }
    Animation lastAnimationPlayed() { return _lastAnimationPlayed; }

    int    timeSinceLastAnimation() { return (_timeAnimation < 0) ? _timeAnimation : (int)(millis() - _timeAnimation); }
    int    timeSinceLastReplay() { return (_timeReplay < 0) ? _timeReplay : (int)(millis() - _timeReplay); }
    int    timeSinceLastDreaming() { return (_timeDreaming < 0) ? _timeDreaming : (int)(millis() - _timeDreaming); }
    int    timeSinceLastIdleSolve() { return (_timeIdleSolve < 0) ? _timeIdleSolve : (int)(millis() - _timeIdleSolve); }
    int    timeSinceLastBatteryAnimation() { return (_timeBatteryAnimation < 0) ? _timeBatteryAnimation : (int)(millis() - _timeBatteryAnimation); }
    void   setAnimation(Animation anim)
        {
        if (anim == Animation::ANIM_NONE) return;
        _lastAnimationPlayed = anim;
        _timeAnimation = millis();
        switch (anim)
            {
            case Animation::ANIM_REPLAY:    _nbAnimationsReplay++;    _timeReplay = _timeAnimation; break;
            case Animation::ANIM_DREAMING:  _nbAnimationsDreaming++;  _timeDreaming = _timeAnimation; break;
            case Animation::ANIM_IDLESOLVE: _nbAnimationsIdleSolve++; _timeIdleSolve = _timeAnimation; break;
            default: break;
            }
        }

    bool replayCubeAvailable() { return (Memory::previous_solve_moves[0] != 0); }

    };



static SarcasmState state; // the main sarcasm state. 


#define MIN_TOUCH_DELAY 100 // minimum delay (ms) after which a touch is considered valid (to avoid false touches right after end of speech).


const char MOOD_CURIOUS_STR[] PROGMEM = "curious";
const char MOOD_PLAYFUL_STR[] PROGMEM = "playful";
const char MOOD_LOGIC_STR[] PROGMEM = "logic";
const char MOOD_EXISTENTIAL_STR[] PROGMEM = "existential";
const char MOOD_HAUNTING_STR[] PROGMEM = "haunting";
const char MOOD_DRYLOGIC_STR[] PROGMEM = "drylogic";
const char MOOD_MOCKING_STR[] PROGMEM = "mocking";
const char* const MOOD_NAMES[] PROGMEM = { MOOD_CURIOUS_STR, MOOD_PLAYFUL_STR, MOOD_LOGIC_STR, MOOD_EXISTENTIAL_STR, MOOD_HAUNTING_STR, MOOD_DRYLOGIC_STR, MOOD_MOCKING_STR };



/**
* Make a solve. 
**/
int mainloop_makeSolve()
    {
    while(1)
        {
        int dif, nbm;
        const int r = solveCube(dif, nbm); // go solve the cube. 
        state.setSolve(dif, nbm); // save the result. 
        if (r != CODE_SPINNED) 
            { 
            if (MAX98357A::isSpeaking()) { ABORT("Impossible 1"); }
            return CODE_SPINNED;  // *** may return r instead but ignore and always return CODE_SPINNED for the time being         
            } 
        state.setInput(CODE_SPINNED); // set the input code to spinned
        }
    }




/**
* Wait for speech to end before returning.
* 
* Returns
* 
*    CODE_NOTHING        : speech completed, no input detected.
*    CODE_SPINNED        : the cradle was spinned. Return immediately, speech may still be going on.
*    CODE_TOUCHED_SCREEN : the screen was touched. Return immediately or not, depending on interrupt_on_touch.
*    CODE_CHARGING_START / CODE_CHARGING_STOP: charging started. This code may only be returned if 'interrupt_on_charging' is set (and then return immediately, speech may be ongoing).
**/
SLOWFUN int mainloop_waitEndSpeech(bool interrupt_on_touch, bool interupt_on_charging)
    {
    const uint32_t lt = Display::touchedTime(); // time of last touch
    while (MAX98357A::isSpeaking())
        {
        if (CraddleMove::status() == 2) { state.setInput(CODE_SPINNED); return mainloop_makeSolve(); }
        if (interupt_on_charging)
            {
            const int st = FBSensors::chargeStatus();
            if ((st == CODE_CHARGING_START) || (st == CODE_CHARGING_STOP)) { state.setInput(st); return st; }
            }
        if (interrupt_on_touch)
            {
            if (Display::touchedTime() > lt + MIN_TOUCH_DELAY) { state.setInput(CODE_TOUCHED_SCREEN); return CODE_TOUCHED_SCREEN; }
            }
        graphics3D::updateAll(0); // redraw the screen
        threads.yield(); 
        }
    if (CraddleMove::status() == CODE_SPINNED) { state.setInput(CODE_SPINNED); return mainloop_makeSolve(); }
    if (Display::touchedTime() > lt + MIN_TOUCH_DELAY) { state.setInput(CODE_TOUCHED_SCREEN); return CODE_TOUCHED_SCREEN; }
    return CODE_NOTHING;
    }



/** Pause for a given number of milliseconds. */
SLOWFUN int mainloop_pause(int ms, bool interrupt_on_touch, bool interupt_on_charging)
    {
    MAX98357A::audioLed.setDriver(MAX98357A::AudioLed::DRIVER_VOICE); // set the audio LED driver to voice mode
    elapsedMillis em = 0;
    const uint32_t lt = Display::touchedTime(); // time of last touch
    while (((int)em) < ms)
        {
        if (CraddleMove::status() == 2) { state.setInput(CODE_SPINNED); return mainloop_makeSolve(); }
        if (interupt_on_charging)
            {
            const int st = FBSensors::chargeStatus();
            if ((st == CODE_CHARGING_START) || (st == CODE_CHARGING_STOP)) { state.setInput(st); return st; }
            }
        if (interrupt_on_touch)
            {
            if (Display::touchedTime() > lt + MIN_TOUCH_DELAY) { state.setInput(CODE_TOUCHED_SCREEN); return CODE_TOUCHED_SCREEN; }
            }
        graphics3D::updateAll(0); // redraw the screen
        threads.yield();
        }
    if (CraddleMove::status() == CODE_SPINNED) { state.setInput(CODE_SPINNED); return mainloop_makeSolve(); }
    if (Display::touchedTime() > lt + MIN_TOUCH_DELAY) { state.setInput(CODE_TOUCHED_SCREEN); return CODE_TOUCHED_SCREEN; }
    return CODE_NOTHING;
    }


/**
* Speak a text and output it on the console then wait for the end of speech and then wait for an additional 
* add_ms milliseconds before returning.
* 
* Returns
* 
*    CODE_NOTHING        : speech completed, no input detected.
*    CODE_SPINNED        : the cradle was spinned. Return immediately, speech may still be going on.
*    CODE_TOUCHED_SCREEN : the screen was touched. Return immediately or not, depending on interrupt_on_touch.
*    CODE_CHARGING_START / CODE_CHARGING_STOP: charging started/stopped.
**/
SLOWFUN int mainloop_speechAnimation(const char* message, int skip_lines, bool interrupt_on_touch, bool interupt_on_charging)
    {
    if (skip_lines > 0)
        {
        MAX98357A::stopSpeak();  // just in case, stop any ongoing speech
        for (int i = 0; i < skip_lines; i++) { Console::console.print("\n"); }
        }
    MAX98357A::audioLed.setDriver(MAX98357A::AudioLed::DRIVER_VOICE); // set the audio LED driver to voice mode
    MAX98357A::setAudioLevelVoice();
    MAX98357A::speak(message); // speak the message
    state.incSpeechSameMood();
    int r = mainloop_waitEndSpeech(interrupt_on_touch, interupt_on_charging);
    if (MAX98357A::isSpeaking())
        { // interrupted...
        MAX98357A::stopSpeak();
        Console::console.print("...\n\n");
        return r;
        }
    Console::console.print("\n\n");
    if (r != CODE_NOTHING)
        { // an input was detected just as the speech ended
        return r;
        }
    return r;
    }


SLOWFUN int mainloop_speechAnimationRandom(int skip_lines, bool interrupt_on_touch, bool interupt_on_charging)
    {
    int ev = 0;
    Mood cm = state.currentMood(); 
    if ((cm != Mood::MOOD_CURIOUS)&&(cm != Mood::MOOD_MOCKING))
        {
        ABORT("impossible: mood " << MOOD_NAMES[(int)cm]);
        }
    if (cm == Mood::MOOD_CURIOUS)
        { 
        const int n_c = sentences::picker_curious.size(); 
        const int n_p = sentences::picker_playful.size();
        const int n_l = sentences::picker_logic.size();
        const int n_e = sentences::picker_existential.size();
        const int n_h = sentences::picker_haunting.size();
        const int tot = n_c + n_p + n_l + n_e + n_h;
        const int a = rng::rand(0, tot);
        if (a < n_c)
            {
            DEBUG("Current mood 'curious': playing picker 'curious'");
            ev = mainloop_speechAnimation(sentences::picker_curious.next_str(), skip_lines, interrupt_on_touch, interupt_on_charging);
            }
        else if (a < n_c + n_p)
            {
            DEBUG("Current mood 'curious': playing picker 'playful'");
            ev = mainloop_speechAnimation(sentences::picker_playful.next_str(), skip_lines, interrupt_on_touch, interupt_on_charging);
            }
        else if (a < n_c + n_p + n_l)
            {
            DEBUG("Current mood 'curious': playing picker 'logic'");
            ev = mainloop_speechAnimation(sentences::picker_logic.next_str(), skip_lines, interrupt_on_touch, interupt_on_charging);
            }
        else if (a < n_c + n_p + n_l + n_e)
            {
            DEBUG("Current mood 'curious': playing picker 'existential'");
            ev = mainloop_speechAnimation(sentences::picker_existential.next_str(), skip_lines, interrupt_on_touch, interupt_on_charging);
            }
        else
            {
            DEBUG("Current mood 'curious': playing picker 'haunting'");
            ev = mainloop_speechAnimation(sentences::picker_haunting.next_str(), skip_lines, interrupt_on_touch, interupt_on_charging);
            }   
        }
    else
        {
        const int n_m = sentences::picker_mocking.size();
        const int n_d = sentences::picker_drylogic.size();
        const int tot = n_m + n_d;
        const int a = rng::rand(0, tot);
        if (a < n_m)
            {
            DEBUG("Current mood 'mocking': playing picker 'mocking'");
            ev = mainloop_speechAnimation(sentences::picker_mocking.next_str(), skip_lines, interrupt_on_touch, interupt_on_charging);
            } 
        else
            {
            DEBUG("Current mood 'mocking': playing picker 'drylogic'");
            ev = mainloop_speechAnimation(sentences::picker_drylogic.next_str(), skip_lines, interrupt_on_touch, interupt_on_charging);
            }
        }
    return ev;
    }



/** Perform a tag animation: 'general tag' **/
SLOWFUN int mainloop_tagAnimation_general(int skip_lines, bool stop_on_craddle_spin, bool stop_on_charge_event)
    {
    if (skip_lines > 0)
        {
        MAX98357A::stopSpeak();  // just in case, stop any ongoing speech
        for (int i = 0; i < skip_lines; i++) { Console::console.print("\n"); }
        }
    int r = transition_tags::play_transition_tag_general(true, stop_on_craddle_spin, stop_on_charge_event);
    if (r != CODE_NOTHING) { state.setInput(r); }
    if (r == CODE_SPINNED) { return mainloop_makeSolve(); }
    return r;
    }


/** Perform a tag animation: 'switching tag' **/
SLOWFUN int mainloop_tagAnimation_switching(int skip_lines, bool stop_on_craddle_spin, bool stop_on_charge_event)
    {
    if (skip_lines > 0)
        {
        MAX98357A::stopSpeak();  // just in case, stop any ongoing speech
        for (int i = 0; i < skip_lines; i++) { Console::console.print("\n"); }
        }
    int r = transition_tags::play_transition_tag_switching(true, stop_on_craddle_spin, stop_on_charge_event);
    if (r != CODE_NOTHING) { state.setInput(r); }
    if (r == CODE_SPINNED) { return mainloop_makeSolve(); }
    return r;
    }


/** Perform a tag animation: 'enter agressive tag' **/
SLOWFUN int mainloop_tagAnimation_enter_aggressive(int skip_lines, bool stop_on_craddle_spin, bool stop_on_charge_event)
    {
    if (skip_lines > 0)
        {
        MAX98357A::stopSpeak();  // just in case, stop any ongoing speech
        for (int i = 0; i < skip_lines; i++) { Console::console.print("\n"); }
        }
    int r = transition_tags::play_transition_tag_enter_aggressive(true, stop_on_craddle_spin, stop_on_charge_event);
    if (r != CODE_NOTHING) { state.setInput(r); }
    if (r == CODE_SPINNED) { return mainloop_makeSolve(); }
    return r;
    }


/** Perform a tag animation: 'exit agressive tag' **/
SLOWFUN int mainloop_tagAnimation_exit_aggressive(int skip_lines, bool stop_on_craddle_spin, bool stop_on_charge_event)
    {
    if (skip_lines > 0)
        {
        MAX98357A::stopSpeak();  // just in case, stop any ongoing speech
        for (int i = 0; i < skip_lines; i++) { Console::console.print("\n"); }
        }
    int r = transition_tags::play_transition_tag_exit_aggressive(true, stop_on_craddle_spin, stop_on_charge_event);
    if (r != CODE_NOTHING) { state.setInput(r); }
    if (r == CODE_SPINNED) { return mainloop_makeSolve(); }
    return r;
    }


/** Perform a dreaming animation **/
int mainloop_dreamingAnimation()
    {
    int r = dreamingAnimation();
    state.setAnimation(Animation::ANIM_DREAMING);
    if (r != CODE_NOTHING) { state.setInput(r); }
    if (r == CODE_SPINNED) { return mainloop_makeSolve(); }
    return r;
    }


/** Perform a dreaming animation **/
int mainloop_idleSolveAnimation()
    {
    int r = idleSolveAnimation();
    state.setAnimation(Animation::ANIM_IDLESOLVE);
    if (r != CODE_NOTHING) { state.setInput(r); }
    if (r == CODE_SPINNED) { return mainloop_makeSolve(); }
    return r;
    }


/** Perform a repeat solving animation **/
int mainloop_repeatSolvingAnimation()
    {
    int r = repeatSolvingAnimation();
    state.setAnimation(Animation::ANIM_REPLAY);
    if (r != CODE_NOTHING) { state.setInput(r); }
    if (r == CODE_SPINNED) { return mainloop_makeSolve(); }
    return r;
    }


/** Perform a battery animation **/
int mainloop_batteryAnimation(int code)
    {
    int r = batteryAnimation(code, false);    
    if (r != CODE_NOTHING) { state.setInput(r); }
    if (r == CODE_SPINNED) { return mainloop_makeSolve(); }
    return r;
    }


/** Perform the shutdown sequence **/
int mainloop_shutdownSequence()
    {
    int r = shutDownSequence();
    state.setInput(r); 
    if (r == CODE_SPINNED) { return mainloop_makeSolve(); }
    return r;
    }










#define MIN_MOOD_SPEECH 2
#define MAX_MOOD_SPEECH 4
#define MOOD_CHANGE_PROB (0.5f)

#define PROB_SKIP_SPEECH (0.3f)

int previous_nb_tags = 0; // number of tags played the previous time. 
bool skipped_speech = true; 
bool never_skipped_speech = true;

#define MIN_WAIT 2000
#define MAX_WAIT 4500

#define MIN_WAIT_SMALL 1000
#define MAX_WAIT_SMALL 2500


#define IDLE_TIME_SHUTDOWN (180*1000) // shutdown after 4 minute or idleness

int nextWait = -1;  // -1 iss long, -2 is short

#define BATTERY_STATUS_PERIOD_MS (60*1000)
elapsedMillis batteryStatus_ms; // time of last battery message
bool battery_normal_shown = false; // true if the normal battery status has been shown at least once.
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

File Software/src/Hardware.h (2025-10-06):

//
// Copyright 2021 Arvind Singh
//
// This file is part of the S.A.R.C.A.S.M. source code.
//
// This is a free software: you can redistribute it and/or modify
// it under the terms of the GNU General Public License as published by
// the Free Software Foundation, either version 3 of the License, or
// (at your option) any later version.
//
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
#pragma once


/****************************************************************************************************************
 * 
 * PINOUT FOR V1.2 (2024)
 * 
*****************************************************************************************************************/


/***********************************************************************************
*
* Hardware resources 
* 
*  Thread:
* 
*  [GPT1]                        : used by teensyThread
* 
*  Sensors:
*  
*  [128] QUADTIMER1 (TMR1)       : periodic sensor interrupt
*                                : -> read voltages/current/servo positions/craddle position
*                                : -> overvoltage/undervoltage protection
*                                
*  Servos et stepper:
*  
*  [80] QUADTIMER3 (TMR3)        : Servos Grip & Tumble (PWM generation)
*  
*  [64] GPT2                     : Stepper motor DRV8834 (Pulse generation)
*   
*  Outputs:
*  
*  [128] DMA interrupt           : OctoWS2811 Led strip driver.
*  [128] QUADTIMER4              : 
*  
*  [144] PIT (x1)                : ILI9341_T4 (screen driver)
*  [144] SPI FIFO interrupt      :
*  [144] DMA interrupt           :
* 
*  
*  SDcard and Audio playback ? 
* 
*  [144] QUADTIMER2 : playing the sequence ? 
* 
* Audio lib ? 
* 
* 
* Panic handler 
* [224] RTC 125ms : check for panic. IRQ_SNVS_IRQ
* 
************************************************************************************/




/***********************************************************************************
* 
* Pinout for the TeensyRubik v1.1 board.
*
* c.f. the schematic for details. 
*
************************************************************************************/



/***************************************
* PANIC
****************************************/
#define PANIC_IRQ_PRIORITY 224
#define PANIC_IRQ_NAME IRQ_SNVS_IRQ
#define PANIC_TIMER_NAME TeensyTimerTool::RTC
#define PANIC_PERIOD_US 15625 // 15625us = 16ms (64Hz)


/***************************************
* CURRENT FEEDBACK SENSORS
****************************************/
#define FBSENSORS_PERIOD_US 2500                        // poll every 2.5ms = 400Hz
#define FBSENSORS_NBSKIP_VOLTAGE 10                     // skip 10 polls before reading the voltage/current

#define FBSENSORS_TIMER_NAME    TeensyTimerTool::TMR1   // timer used for the feedback sensors
#define FBSENSORS_IRQ_NAME      IRQ_QTIMER1             // name of the associated IRQ
#define FBSENSORS_ADJUST_TIMER_FOR_OVERCLOCK 1          // **** correct the frequency when overclocking the teensy. Must be 1 when using QuadTimer (TMR) and 0 when using PIT Timer
#define FBSENSORS_IRQ_PRIORITY  128                     // priority the interrupt

#define FBSENSORS_ADC_AVERAGING        32                                  // 
#define FBSENSORS_ADC_RESOLUTION       12                                  //  
#define FBSENSORS_ADC_CONVERSION_SPEED ADC_CONVERSION_SPEED::MED_SPEED     //
#define FBSENSORS_ADC_SAMPLING_SPEED   ADC_SAMPLING_SPEED::MED_SPEED       //

#define FBSENSORS_I2C_SPI_SPEED         1000000                             // 1MHz
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

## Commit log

2025-10-06 Add note on Teensy core modification requirements
    Added note about Teensy core modification for RAM fitting.
2025-11-01 Update README with Teensy forum link
    Added a link to the Teensy forum thread for additional details.
2025-11-01 added STL files.
    [AS5600_holder.stl, AS5600_holder_cover.stl, SARCASM_nametag_multicolor.stl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]
